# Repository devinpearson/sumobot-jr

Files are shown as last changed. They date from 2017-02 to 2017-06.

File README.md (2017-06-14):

# Makerlabs Sumobot.

Makerlabs Sumobot is a forked open source sumobot design by [@makenai]. We kept the design similar but added a few new cut outs to allow some line sensors and a proximity sensor in the scoop. The Makerlabs Sumobot is intended to be a autonomous fighting bot, using it as a platform for other autonomous challenges like mazes.

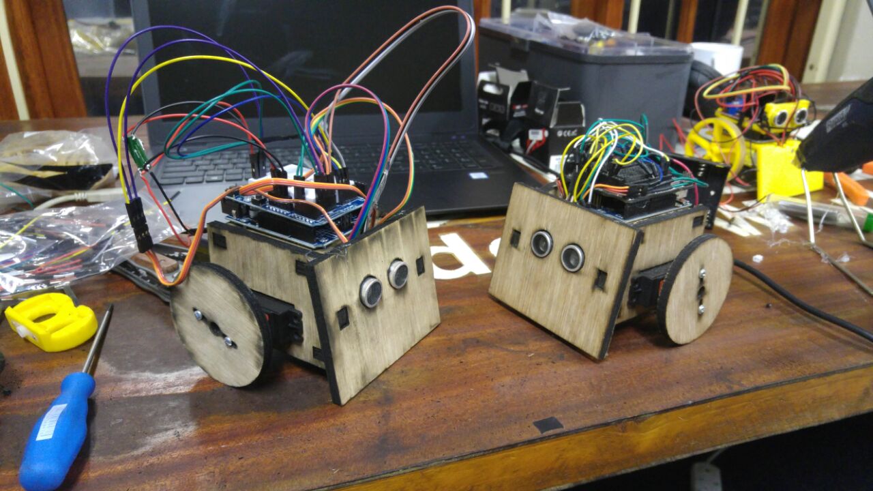
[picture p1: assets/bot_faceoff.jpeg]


## How ?

If you're planning on laser cutting the bots, you should use the OpenSCAD source file to generate a cutting plan for your specific type of laser cutter and material thickness. There's a wiki article for that!

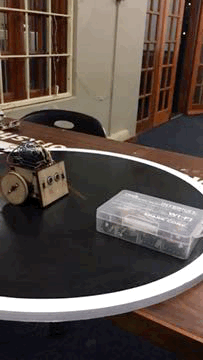
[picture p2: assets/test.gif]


[Laser Cutting with the OpenSCAD file](https://github.com/makenai/sumobot-jr/wiki/Working-with-the-OpenSCAD-file)

If you want to jump right into it, you can watch this instructional video, but note that you may not want to clip the wires if you plan to reuse the servos for something else:

[Sumobot Jr Assembly video for Nodebots Day 7/27](http://www.youtube.com/watch?v=0Q3hrKUwxDM)

[IKEA-style Assembly Instruction Card](http://makenai.github.io/sumobot-jr/sumobot-instructions.pdf)

[Katie K's No Solder Guide](http://katiek2.github.io/sumobot-nosolder/)

[Frank Hunleth's Arduino Mini Shield](https://oshpark.com/shared_projects/TEsKZkdg)

The main part of the design is a cutting sheet in EPS file format that is designed to be used with a laser cutter. You can find it in the cutting_plans directory. If you don't have a laser cutter, you can use a CNC, tape your printout to balsa wood and go at it with an x-acto knife, or send it to a laser cutting service like [Ponoko](https://www.ponoko.com/) and get the sheet done for about $10.

There is also a directory called 3d_print that contains an STL file for a ball caster designed by [sliptonic](http://www.thingiverse.com/thing:13782) - the STL is set up for a 16mm ball bearing, but you can make one for other sizes with the included OpenSCAD file.

## What if I don't have a Laser Cutter / 3D Printer?!

Neither do I! The best way to get some help creating the parts is to look up your local [Hackerspace or Makerspace ](http://hackerspaces.org) and connect with them. Our Johannesburg makerspace called [Makerlabs](http://makerlabs.co.za) hosted at [Made In Workshop](http://madeinworkshop.co.za/)

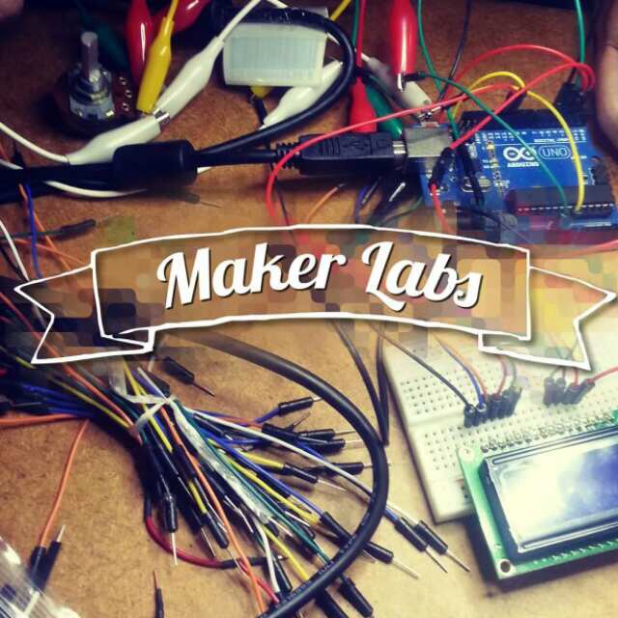
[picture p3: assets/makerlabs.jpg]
[](http://makerlabs.co.za)

If you don't have a hackerspace nearby, you can also use a mail order service like [Ponoko](http://ponoko.com) that does both 3D printing and laser cutting.

## Other Parts Needed

+ [Arduino](https://www.robotics.org.za/arduino-boards-and-accessories.html/arduino-uno-r3.html) - R189
+ [4xAA battery holder](https://www.robotics.org.za/battery-holder-4xaa.html?search=battery%20holder) - R18
+ 2 Cable ties 4.7 x198mm works well Hellermann Tyton T50R - ?
+ 5 3.0 x 12mm wood screws Eureka - ?
+ Thick rubber bands [Croxley No 64] - ?
+ 2 continuous servo motors [Power AR-3606HB](https://www.robotics.org.za/servo-motors-1821899125/power-hd-continuous-rot-servo-6-7kg-cm.html) - R225
+ Some wire or leads
+ 16mm steel ball from a Bearing shop like BMG - ~R6

## Wiring Diagram (thanks @Buglish)

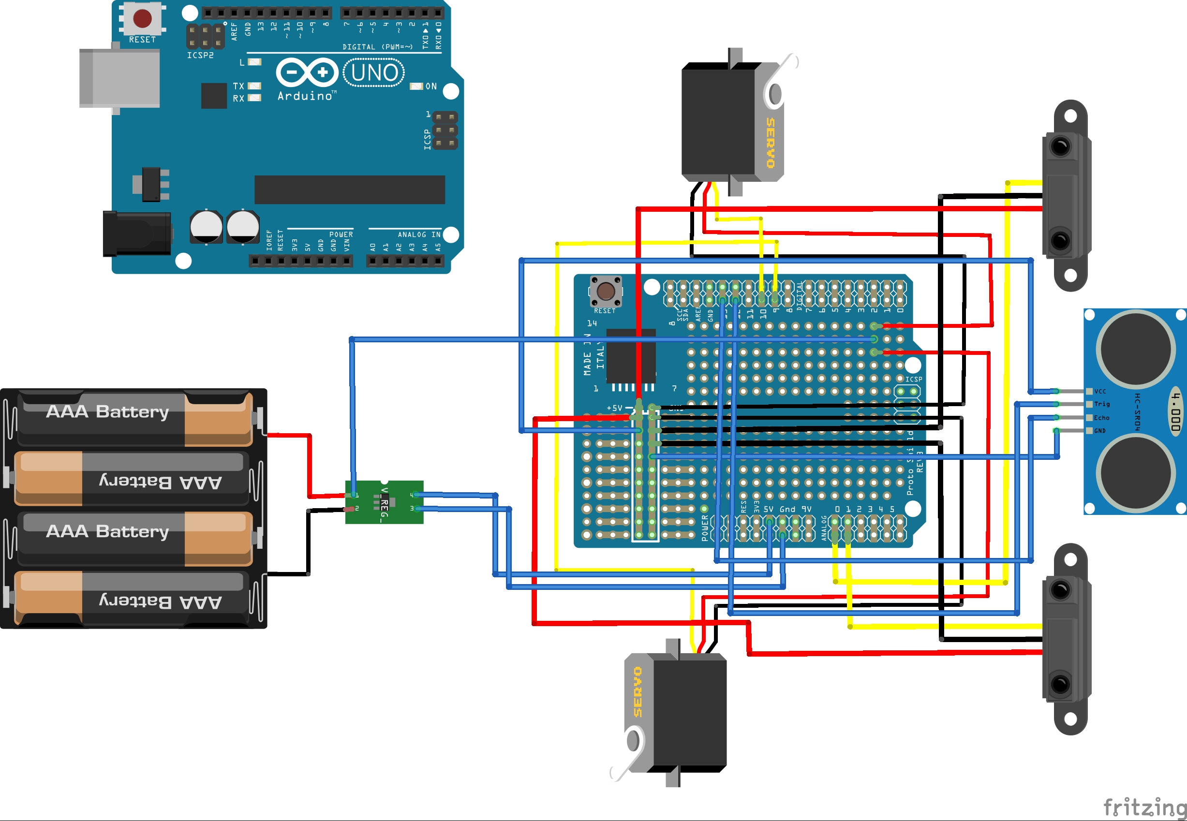
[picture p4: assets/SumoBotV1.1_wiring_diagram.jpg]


That's about it! Connect the red and black leads on the servos together, then connect them to the + and - terminals on the battery holder respectively. Then connect the black leads and - terminal to the ground of the Arduino. Finally, the white leads of each motor go to pins 9 and 10 (or whatever you like) on the Arduino - you're done!

## Sample Code

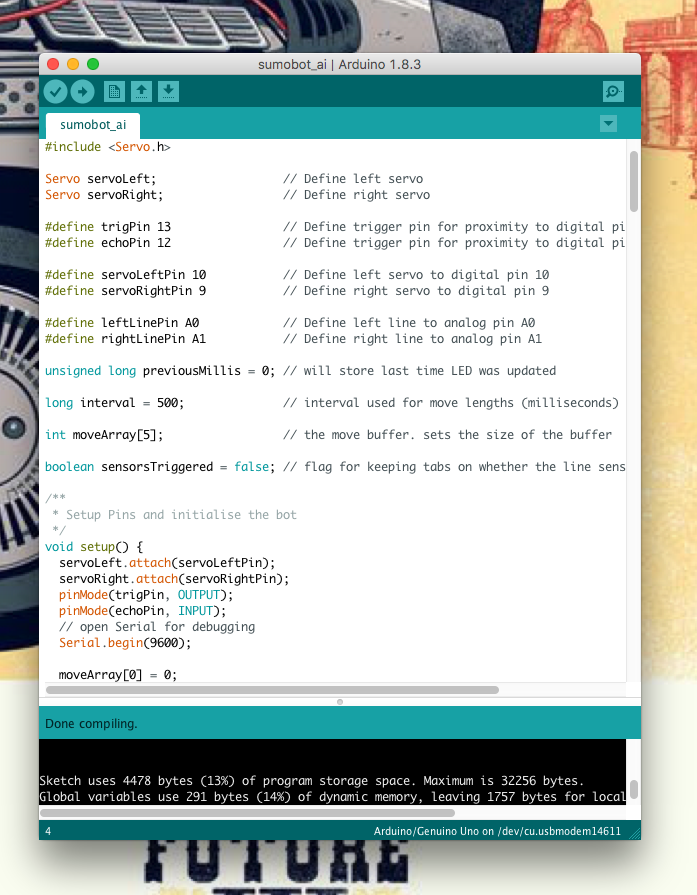
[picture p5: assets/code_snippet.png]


To run the sample code. just upload any of the sketches in the code_examples/arduino folder

Robot Sumo league

[illustrated Rules by Robot Room](http://www.robotroom.com/SumoRules.html)

## License

[Creative Commons - Attribution - ShareAlike 3.0](http://creativecommons.org/licenses/by-sa/3.0/)

You are free to:

+ to Share — to copy, distribute and transmit the work, and
+ to Remix — to adapt the work
+ Under the following conditions:
    + Attribution — You must attribute the work in the manner specified by the author or licensor (but not in any way that suggests that they endorse you or your use of the work)
    + Share Alike — If you alter, transform, or build upon this work, you may distribute the resulting work only under the same, similar or a compatible license.

With the understanding that:

+ Waiver — Any of the above conditions can be waived if you get permission from the copyright holder.
+ Other Rights — In no way are any of the following rights affected by the license:
    + your fair dealing or fair use rights;
    + the author's moral rights; and
    + rights other persons may have either in the work itself or in how the work is used, such as publicity or privacy rights.

## Credits

Made by



Design by [@makenai](http://twitter.com/makenai) with feedback and ideas from [@noopkat](http://twitter.com/noopkat) aka (by their powers combined) Amalgamation of Cats.

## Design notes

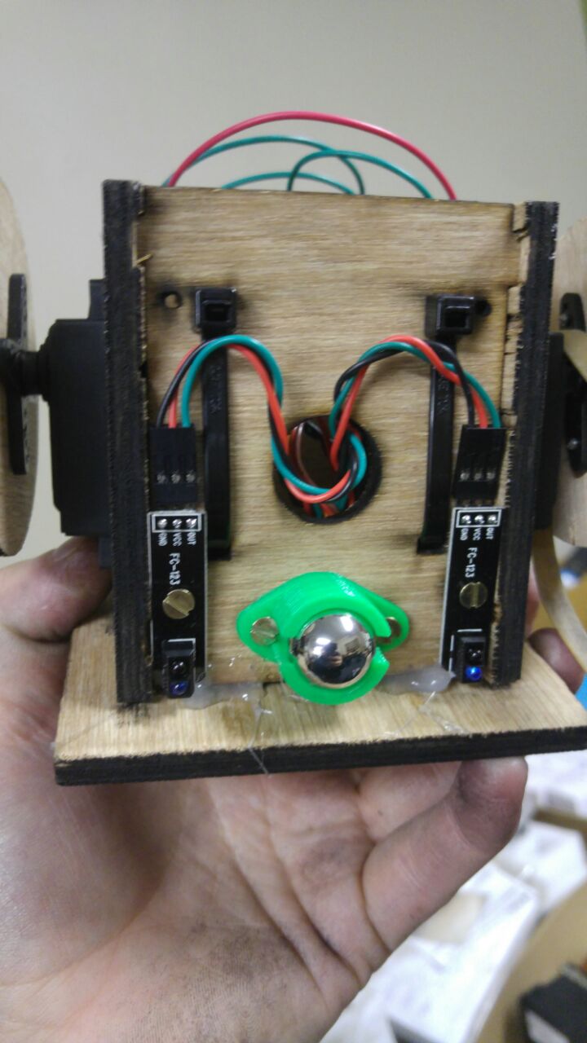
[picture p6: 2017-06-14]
assets/under_bot.jpeg

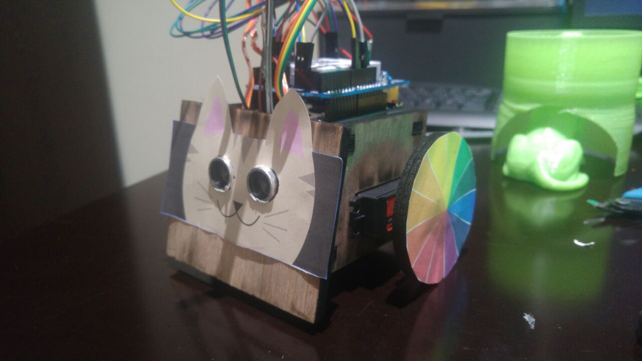
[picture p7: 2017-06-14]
assets/Meow_sumobot.jpeg

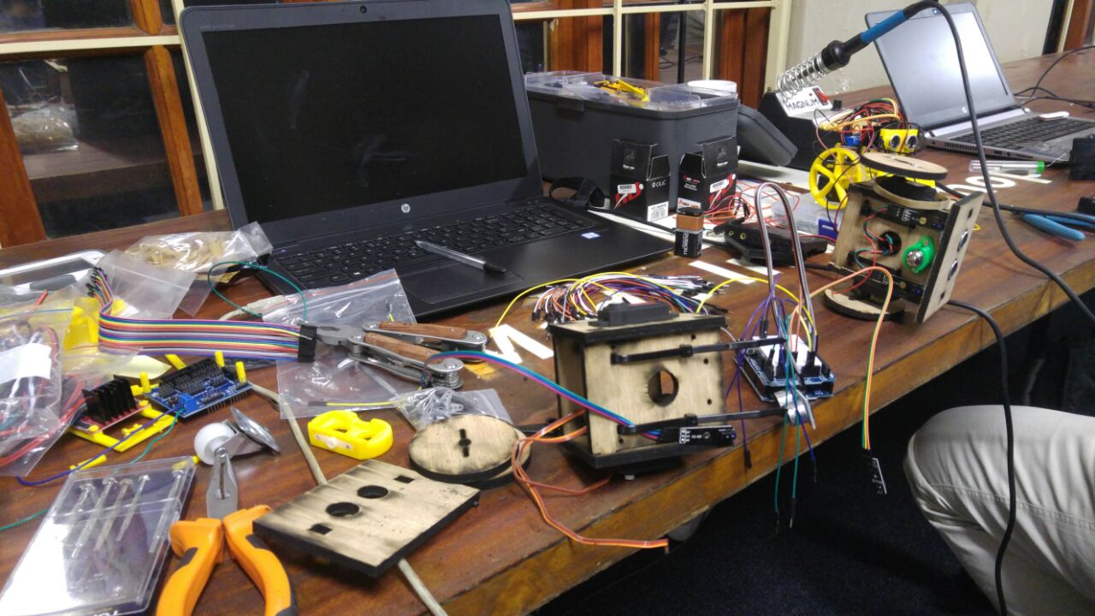
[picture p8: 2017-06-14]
assets/mounting_servos.jpeg

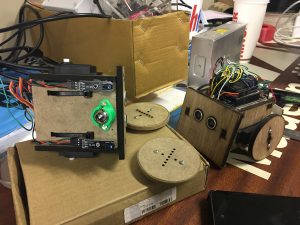
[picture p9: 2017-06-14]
assets/IMG_7833-300x225.jpg

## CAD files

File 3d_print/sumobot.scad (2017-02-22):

/*
 * =============================================================================
 * SumoBot Kit Master OpenSCAD File
 * =============================================================================
 * All measurements are in mm, because go metric or go home.
 */

 /* Build Flags - Variables to programatically select which part to output */

  build_laser_sheet = 1;
  build_wheel = 0;
  build_top = 0;
  build_shovel = 0;
  build_bottom = 0;
  build_side = 0;

/* Features Flags */

  // For 3D printing, we can have a curved or flat shovel
  curved_shovel = 0;

  // For 3D printing, we can include a ball caster on the bottom
  built_in_caster = 0;

  // For 3D printing, we can have a built in wheel hub
  built_in_hub = 1;

  // For 3D printing, we can select a pinoccio mount for the top
  pinoccio_top = 0;

/* Parameters */

  // Kerf is the amount of space removed by a cutting tool. I use it
  // here to describe how much space to leave between tabs and space.
  // For laser cutters, I use 0.05, for 3D printers I use 0.375
  kerf = 0.05;

  // How thick is the material? This also is the tab height.
  material_thickness = 6;

  // How high is the battery case?
  battery_case_height = 20;

  // How large is our servo hole?
  servo_height = 21.5;
  servo_length = 42.5;

  // How long is the sumo bot?
  sled_length = 80.5;

  // How wide is the sumo bot?
  sled_width = 66;

  // How close to the edge of the material do we place a tab?
  tab_edge_distance = 5;

  // How long are our tabs?
  tab_length = 10;

  // What is the angle that the sumobot shovel?
  ramp_angle = 80;

  // How wide is the shovel?
  shovel_width = 100;

  // How high is the shovel?
  shovel_height = 70;

  // Only for a 3D printed, curved shovel, how tall is the side?
  shovel_side_height = 20;

  // How big are our ziptie holes?
  ziptie_height = 5;
  ziptie_width = 2.5;

  // How big are the screw holes? 2.25mm is good for #4 wood screws
  screw_diameter = 2.25;

  // How far apart are our ball caster holes?
  caster_screw_spacing = 25;

  // How far back from the front do we place the caster?
  caster_position = 12;

  // How big are our wheels?
  wheel_radius = 35;

  // Caster Settings
  Caster_WallThickness = 2;
  Caster_BallSize = 12.5;
  Caster_Airgap = .5;
  Caster_TotalHeight = 14;
  Caster_BallProtrude = .33;

  // Servo Wheel
  SERVO_HEAD_CLEAR = 0.2;
  FUTABA_3F_SPLINE = [
      [6, 4, 1.1, 2.5],
      [25, 0.3, 0.7, 0.1]
  ];
  FUTABA_3F_SPLINE_KERF = [
      [6-(kerf/2), 4, 1.1, 2.5],
      [25, 0.3, 0.7, 0.1]
  ];
  
  // Wire Management
  wire_management = 1;
  wire_management_width = 30;

/* Calculated Values */

  // Tab spacing account for kerf
  tab_spacing = kerf * 2;

  // We figure out the side based on a snug fit for the battery case
  sled_height = ((material_thickness + tab_edge_distance) * 2 ) +
  	servo_height + battery_case_height;

  // Length of the ramp (bottom of the right triangle) depends on the angle
  ramp_length = cos( ramp_angle ) * sled_height;

  // We want to place the tab the correct tab distance on the bottom, so we need
  // to cut into the distance taken up by the ramp.
  ramp_tab_distance = cos(ramp_angle)*( tab_edge_distance + material_thickness);

  // The length of the sled plus the length of the ramp
  side_length = sled_length + ( cos( ramp_angle ) * (sled_height - tab_edge_distance) );

/* Utility Modules */

// A hole for a screw.
module screw_hole() {
	circle(d=screw_diameter);
}

// Male side of the tab
module tab() {
	square([tab_length, material_thickness]);
}

// Female side of the tab
module tab_hole() {
    // removed the tab spacing as its not a tight fit
	translate([tab_spacing/-2,tab_spacing/-2])
		//square([tab_length + tab_spacing, material_thickness +tab_spacing]);
		square([tab_length, material_thickness]);
}

// A ziptie hole
module ziptie_hole() {
	square([ziptie_width,ziptie_height]);
}

// Built-in ball caster
module caster() {
	cylheight = Caster_TotalHeight;
	cylrad = (Caster_BallSize/2) + Caster_WallThickness + Caster_Airgap;
	difference () {
		cylinder(r1 = cylrad , r2 = cylrad,  cylheight - (Caster_BallSize*Caster_BallProtrude));
		translate([0,0,Caster_TotalHeight - Caster_BallSize/2]) {
			cube(size = [cylrad*2+5, cylrad/2, Caster_BallSize*1.25], center = true );
		}
		translate([0,0,Caster_TotalHeight - (Caster_BallSize/2)]) {
			sphere (Caster_BallSize/2+Caster_Airgap, $fa=5, $fs=0.1);
		}
	}
}

// Servo mounting hole including a circular cutout for the wires
module servo_hole() {
	square([servo_length, servo_height]);
	// screw holes
	//translate([-4.5,(servo_height/2)+5])
	//	screw_hole();
	//translate([-4.5,(servo_height/2)-5])
		//screw_hole();
	//translate([servo_length+4.5,(servo_height/2)+5])
		//screw_hole();
	//translate([servo_length+4.5,(servo_height/2)-5])
		//screw_hole();
	// wire hole
	hull() {
		translate([servo_length-1,servo_height/2])
			square(6,center=true);
		translate([servo_length+2.5,servo_height/2])
			circle(3,center=true);
	}

}

// Mounting holes for an arduino
module arduino_holes() {
	translate([-26.05,-24.1]) {
		translate([0, 15.2]) screw_hole();
		translate([0, 43.1]) screw_hole();
		translate([50.8, 0]) screw_hole();
		translate([52.1, 48.2]) screw_hole();
	}
}

// A special pinoccio shaped mount for the top of the bot
module pinoccio_mount() {
	height = 11;
	base_width = 26.5;
	base_length = 45.5;
	bevel_width = 11;
	bevel_length =8.5;
	wall_thickness = 2;
	plug_hole_size = 3.5;

	translate([base_length/-2-bevel_length/-2,-base_width/2])
	difference() {
		linear_extrude(height)
		hull() {
			translate([0,-wall_thickness])
				square([base_length + wall_thickness,base_width + wall_thickness*2]);
 			translate([-bevel_length - wall_thickness,base_width/2-bevel_width/2])
				square(bevel_width);
		}
		translate([0,0,-1])
		linear_extrude(height+2)
		hull() {
			square([base_length,base_width]);
			translate([-bevel_length,base_width/2-bevel_width/2])
				square(bevel_width);
		}
		translate([base_length-1, base_width/2,height])
			rotate([0,90])
			cylinder(r=plug_hole_size,h=wall_thickness+2);
	}
}

// The little curved part on the side of the curved shovel
module sloped_support(size) {
	difference() {
		cube([size,material_thickness,size]);
		translate([size,material_thickness+1,size])
			rotate([90])
			cylinder(r=size-material_thickness,h=material_thickness+2);
	}
}

// Side for a curved shovel (___)
module shovel_side() {
	cube([material_thickness,shovel_height,shovel_side_height]);
	sloped_support(shovel_side_height);
	translate([0,shovel_height-material_thickness])
		sloped_support(shovel_side_height);
}

module servo_head_tooth(length, width, height, head_height) {
    linear_extrude(height = head_height) {
        polygon([[-length / 2, 0], [-width / 2, height], [width / 2, height], [length / 2,0]]);
    }
}

// The little part that you can attach servo hubs to on a servo, used for the
// built in hub option of the wheel.
module servo_head(params, clear = SERVO_HEAD_CLEAR) {

    head = params[0];
    tooth = params[1];

    head_diameter = head[0];
    head_heigth = head[1];

    tooth_count = tooth[0];
    tooth_height = tooth[1];
    tooth_length = tooth[2];
    tooth_width = tooth[3];

	union() {
    cylinder(r = head_diameter / 2 + 0.1, h = head_heigth + 1);

    cylinder(r = head_diameter / 2 - tooth_height + 0.03 + clear, h = head_heigth);

    for (i = [0 : tooth_count]) {
        rotate([0, 0, i * (360 / tooth_count)]) {
            translate([0, head_diameter / 2 - tooth_height + clear, 0]) {
                servo_head_tooth(tooth_length, tooth_width, tooth_height, head_heigth);
            }
        }
    }
	}
}

// The little screw slot in the side of the sumo bot -
module wheel_screw_slot() {
	hull() {
		translate([0,0,-1])
			cylinder(d=screw_diameter,h=material_thickness+2);
		translate([0,8,-1])
			cylinder(d=screw_diameter,h=material_thickness+2);
	}
}

/* Parts */

// The side of the sumobot /___|
module side() {
	linear_extrude(height=material_thickness)
	difference() {

		union() {
			square([sled_length, sled_height]);
			polygon([[0,0], [0,sled_height], [-ramp_length,0]] );
			translate([-ramp_length/2,sled_height/2])
				rotate(ramp_angle)
				translate([-tab_length/2,-0.1])
				tab();
		}

		// Servo hole
		translate([sled_length - servo_length - tab_length - tab_edge_distance - tab_edge_distance,
				material_thickness + tab_edge_distance])
			servo_hole();

		// Bottom right
		translate([sled_length - tab_length - tab_edge_distance, tab_edge_distance])
			tab_hole();

		// Bottom Left
		translate([-ramp_length + ramp_tab_distance + tab_edge_distance,
				tab_edge_distance])
			tab_hole();

		// Top left
		translate([tab_edge_distance, sled_height - material_thickness - tab_edge_distance])
			tab_hole();

		// Top right
		translate([sled_length - tab_length - tab_edge_distance,
				sled_height - material_thickness - tab_edge_distance])
			tab_hole();
	}
}
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

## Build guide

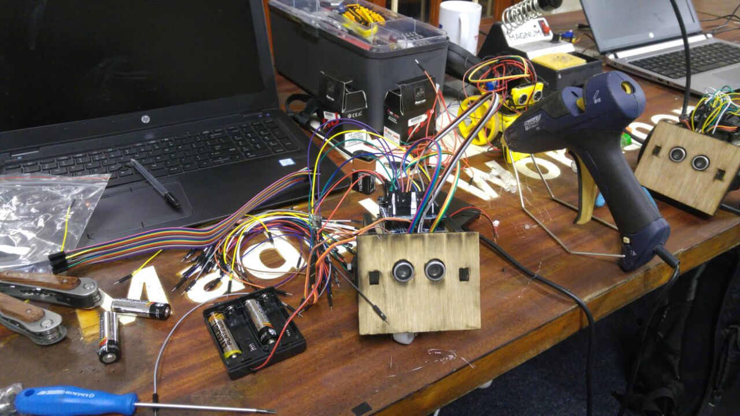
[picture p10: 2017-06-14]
assets/wiring_bot.jpeg

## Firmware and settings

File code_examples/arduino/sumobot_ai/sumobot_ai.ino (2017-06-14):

// Sumobot Sample Code
// Used to get your sumobot in the ring
// Covers most of the basic features and should hold its own in the ring
// Author: Devin Pearson
// License: MIT License (https://opensource.org/licenses/MIT)

#include <Servo.h>

Servo servoLeft;                  // Define left servo
Servo servoRight;                 // Define right servo

#define trigPin 13                // Define trigger pin for proximity to digital pin 12
#define echoPin 12                // Define trigger pin for proximity to digital pin 12

#define servoLeftPin 10           // Define left servo to digital pin 10
#define servoRightPin 9           // Define right servo to digital pin 9

#define leftLinePin A0            // Define left line to analog pin A0
#define rightLinePin A1           // Define right line to analog pin A1

unsigned long previousMillis = 0; // will store last time LED was updated

long interval = 500;              // interval used for move lengths (milliseconds)

int moveArray[5];                 // the move buffer. sets the size of the buffer

boolean sensorsTriggered = false; // flag for keeping tabs on whether the line sensors have been triggered

unsigned long proxPreviousMillis = 0;

  #define proxInterval 750
/**
 * Setup Pins and initialise the bot
 */
void setup() { 
  servoLeft.attach(servoLeftPin);  
  servoRight.attach(servoRightPin);  
  pinMode(trigPin, OUTPUT);
  pinMode(echoPin, INPUT);
  // open Serial for debugging
  Serial.begin(9600);
  
  moveArray[0] = 0;
  makeMove();
  delay(2000);
  moveArray[0] = 5;
} 
/**
 * Main loop
 * keep this as clean as possible to give an overview of what steps are run
 */
void loop() {
  // checks the line sensors
  checkLineSensors();
  // check for an opponent
  readProximity();
  // handles movements
  moveTimer();
  delay(2);
}
/**
 * moveTimer checks if the interval times have passed.
 * if it has it actions the next move
 */
void moveTimer() {
  // gets the current time
  unsigned long currentMillis = millis();

  if (currentMillis - previousMillis >= interval) {
    // save the last time you made a move
    previousMillis = currentMillis;
    // action the next move
    makeMove();
  }

}
/**
 * Checks the proximity sensor for any opponents ahead of it
 */
void readProximity() {

  unsigned long currentMillis = millis();
  if (currentMillis - proxPreviousMillis >= proxInterval) {
       // save the last time you blinked the LED
       proxPreviousMillis = currentMillis;
    long duration, distance;
    // the proximity sensor is triggered by a HIGH pulse of 2 or more microseconds.
    // give a short LOW pulse beforehand to ensure a clean HIGH pulse:
    digitalWrite(trigPin, LOW);
    delayMicroseconds(2);
    digitalWrite(trigPin, HIGH);
    delayMicroseconds(5);
    digitalWrite(trigPin, LOW);
    // get distance in microseconds
    duration = pulseIn(echoPin, HIGH);
    // The speed of sound is 340 m/s or 29 microseconds per centimeter.
    // The ping travels out and back, so to find the distance of the
    // object we take half of the distance travelled.
    distance = duration / 29 / 2;
    
    if (distance >= 70 || distance <= 0){
      Serial.println("Out of range");
    }
    else {
      foundObject();
      Serial.print(distance);
      Serial.println(" cm");
    }
  }
}
/**
 * Checks the line sensors for the edge.
 * If one is triggered the bot will turn the opposite way
 */
void checkLineSensors() {
  // read the pins for the line sensors
  int leftLineValue = analogRead(leftLinePin);
  int rightLineValue = analogRead(rightLinePin);
  // check if either of the seonsors have a value high enough to beconsidered a white line
  if (leftLineValue > 900 || rightLineValue > 900) {
      if (!sensorsTriggered) {
        // turn right
        int direct = 3;
        if (leftLineValue > 900)
        {
          // turn left
          int direct = 4;
        }
        // gives the avoidance commands with direction
        avoidLine(direct);
        // actions the move right away
        makeMove();
        Serial.print("\n line sensor triggered");
        // flag for debounce, needs to wait to be off the line before it can be triggered again
        sensorsTriggered = true;
      }
    } else {
      // turns the flag off again
      sensorsTriggered = false;
    }
}

/**
 * make more thats the command by id from the buffer and matches it to a movement
 */
void makeMove() {
  // we reset the interval timer so actions happen immediately in the moveTimer()
  interval = 0;
  switch(moveArray[0]) {
    case 1:
      forward();
      //Serial.print("\n forward");
      break;
    case 2:
      reverse();
      //Serial.print("\n reverse");
      break;
    case 3:
      turnRight();
      break;
    case 4:
      turnLeft();
      break;
    case 5:
      shortForward();
      //Serial.print("\n forward");
      break;
    case 6:
      turnLeftSlow();
      //Serial.print("\n forward");
      break;
    case 7:
      turnRightSlow();
      //Serial.print("\n forward");
      break;
    default:
      stopRobot();
      break;
  }
  previousMillis = millis();
  // call pop to remove the move we just did
  pop();
}

/**
 * Pop shifts all the movements forward by 1 and added a default command on the end
 */
void pop() {
  moveArray[0] = moveArray[1];
  moveArray[1] = moveArray[2];
  moveArray[2] = moveArray[3];
  moveArray[3] = moveArray[4];
  moveArray[4] = 7;
}

/**
 * Moves forward for 1 second at full pace. 
 * As one servo is backwards we have to send opposite values for the continuous revolution servos
 * 90 is stopped
 * 180 is forward 
 * 0 is backward
 */
void forward() {
  interval = 1000;
  servoLeft.write(0);
  servoRight.write(180);
}

void shortForward() {
  interval = 2000;
  servoLeft.write(0);
  servoRight.write(180);
}

void reverse() {
  interval = 500;
  servoLeft.write(180);
  servoRight.write(0);
}

void turnRight() {
  interval = 300;
  servoLeft.write(180);
  servoRight.write(180);
}
void turnLeft() {
  interval = 300;
  servoLeft.write(0);
  servoRight.write(0);
}
/**
 * This slow command is achieved by having the servo value close to 90.
 * The closer it is the slower the servo will turn
 */
void turnRightSlow() {
  interval = 300;
  servoLeft.write(95);
  servoRight.write(95);
}
void turnLeftSlow() {
  interval = 300;
  servoLeft.write(85);
  servoRight.write(85);
}

void stopRobot() {
  servoLeft.write(90);
  servoRight.write(90);
}
/**
 * runs through some of the basic movements
 */
void demo() {
  moveArray[0] = 1;
  moveArray[1] = 2;
  moveArray[2] = 3;
  moveArray[3] = 4;
  moveArray[4] = 0;
}
/**
 * a left to right motion to search for a target
 */
void sweep() {
  moveArray[0] = 3;
  moveArray[1] = 4;
  moveArray[2] = 3;
  moveArray[3] = 4;
  moveArray[4] = 1;
}
/**
 * used when a line is triggered to move away and face the inside of the arena again
 */
void avoidLine(int direct) {
  moveArray[0] = 2;
  moveArray[1] = direct;
  moveArray[2] = direct;
  moveArray[3] = 0;
  moveArray[4] = 0;
}
/**
 * When a object if found we tell the bot to just keep charging forward
 */
void foundObject() {
  moveArray[0] = 0;
  moveArray[1] = 1;
  moveArray[2] = 1;
  moveArray[3] = 1;
  moveArray[4] = 1;
}
/**
 * use if you want the bot to stop all actions
 */
void stopAll() {
  moveArray[0] = 0;
  moveArray[1] = 0;
  moveArray[2] = 0;
  moveArray[3] = 0;
  moveArray[4] = 0;
  stopRobot();
}

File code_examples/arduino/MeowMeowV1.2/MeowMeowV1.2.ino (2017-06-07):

#include <Servo.h>

Servo servoLeft;          // Define left servo
Servo servoRight;         // Define right servo

#define trigPin 13
#define echoPin 12
#define leftLinePin A0
#define rightLinePin A1
#define proxInterval 750

const int servoLeftInt = 10;
const int servoRightInt = 9;


// defines variables
int distance;
long duration;
int distanceCm, distanceInch;

int leftLineValue=0;
int rightLineValue=0;

boolean targetFound = false;
boolean lineFound = false;

int maxSpeed = 220; // max speed of motors (min 120 -> max 255 ) 
int rotation300mm = 5000; //5000ms sleep to sigify 300 mm
int rotation150mm = 2500; //2500ms sleep to sigify 150 mm
int rotation75mm = 1250; //1250ms sleep to sigify 75 mm
int rotation30mm = 500; //500ms sleep to sigify 30 mm

unsigned long timestampvar = millis();

int buttonPin = 3;
int buttonState = 0; 

boolean started = false;

void setup() {
  delay(2000);
  Serial.begin(9600);
  // motors
  servoLeft.attach(servoLeftInt);  // Set left servo to digital pin 10
  servoRight.attach(servoRightInt);  // Set right servo to digital pin 9
  // sensors
  pinMode(trigPin, OUTPUT);
  pinMode(echoPin, INPUT);
  
  //pinMode(SensorPin,INPUT);
  pinMode(buttonPin, INPUT);

}


void resetSensor(){
   Serial.println("resetSensor");
  // Clears the trigPin
  digitalWrite(trigPin, LOW);
  delayMicroseconds(2);
  //targetFound = false;
}

void virtualDelayStare(int total){
  Serial.println("virtualDelayStare");
  timestampvar = millis();
    while((long(millis())-long(timestampvar)) < long(total)){
        SeekLine();
        seekSensor();
        if(lineFound == true)
            break;
        if(targetFound == false)
            break;
    }
    timestampvar = millis();
}

void virtualDelayFind(int total){
  Serial.println("virtualDelayFind");
  timestampvar = millis();
    while((long(millis())-long(timestampvar)) < long(total)){
        SeekLine();
        seekSensor();
        if(lineFound == true)
            break;
        if(targetFound == true)
            break;
    }
    timestampvar = millis();
}

void goForward(int amount) //backwards
{ 
  Serial.println("GoForward");
  servoLeft.write(0);
  servoRight.write(180);
  virtualDelayStare(amount);
  stopRobot();
} 

void goBackward(int amount) //forwards
{ 
  Serial.println("GoBack");
  servoLeft.write(180);
  servoRight.write(0);
  virtualDelayFind(amount);
  stopRobot();
} 


void seekRight (int turnAmount) //forwards
{ 
  Serial.println("SeekRight");
  servoLeft.write(180);
  servoRight.write(180);
  virtualDelayFind(turnAmount);
  stopRobot();
} 

void seekLeft (int turnAmount) //forwards
{ 
  Serial.println("SeekLeft");
  servoLeft.write(0);
  servoRight.write(0);
  virtualDelayFind(turnAmount);
  stopRobot();
}

void stopRobot() { //stop
  servoLeft.write(90);
  servoRight.write(90);
}

void seekSensor(){
  resetSensor();
  targetFound = false;
  // Sets the trigPin on HIGH state for 10 micro seconds
  digitalWrite(trigPin, HIGH);
  delayMicroseconds(10);
  digitalWrite(trigPin, LOW);

  // Reads the echoPin, returns the sound wave travel time in microseconds
  duration = pulseIn(echoPin, HIGH);
  // Calculating the distance
  //Serial.print("Dur1=");
  //Serial.println(duration);
  distance= duration*0.034/2;
  Serial.print("Distance=");
  Serial.println(distance);
  if(distance > 0 && distance < 30)
    targetFound = true;
}

void SeekLine(){
  lineFound = false;
  leftLineValue = analogRead(leftLinePin);
  rightLineValue = analogRead(rightLinePin);
  
  Serial.print("leftLineValue=");
  Serial.println(leftLineValue);
  Serial.print("rightLineValue=");
  Serial.println(rightLineValue);
  if(leftLineValue > 1000 || rightLineValue > 1000){
    lineFound = true;
    Serial.println("Found");
  } 
  else{
    Serial.println("Not Found");
    lineFound = false;
  }
}

void loop() {
  //Serial.println("--------------------------------------------");

    seekSensor();
    SeekLine();
    if(targetFound == true && lineFound == false){
        goForward(rotation300mm);
    }
    else if(lineFound){
        goBackward(rotation30mm);
    }
    else{
      switch(random(1, 2)) {
          case 1: 
              seekRight(rotation75mm);
              break;
          case 2:
              seekLeft(rotation75mm);
              break;          
      } 
      
    }
}

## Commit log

2017-02-08 added wire management hole
    added wire management hole
    changed wheel size to 70
    made the front shovel bigger
    [sumobot.scad]
2017-02-22 changes to the sumobot layout
    [sumobot.scad]
2017-06-02 Basic wiring diagram - Arduino UNO - Arduino UNO Prototyping shield v5 - 2 Servos - 2 Line Sensors - 1 Ultrasonic Sensor - 1 Battery Pack - 1 Voltage Regulator
2017-06-03 SumoBot v1.1 Diagram correction
    [SumoBotV1.1_wiring_diagram.fzz]
2017-06-14 Removed the node code, moved frizzing diagrams to assets, removed soccer bot
    [SumoBotV1.1_wiring_diagram.fzz, WheelHub.scad, WheelHub.stl]
2017-06-14 Fixed a few errors with avoid lines coming off the arena
    [sumobot_ai.ino]
